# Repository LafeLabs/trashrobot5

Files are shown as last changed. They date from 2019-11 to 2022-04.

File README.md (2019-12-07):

## [link up a level../](../)

# Trash robot

## UNO Shield

[link to page on pcbway to buy board](https://www.pcbway.com/project/shareproject/Generic_Trash_Robot_UNO_Shield__V5.html)

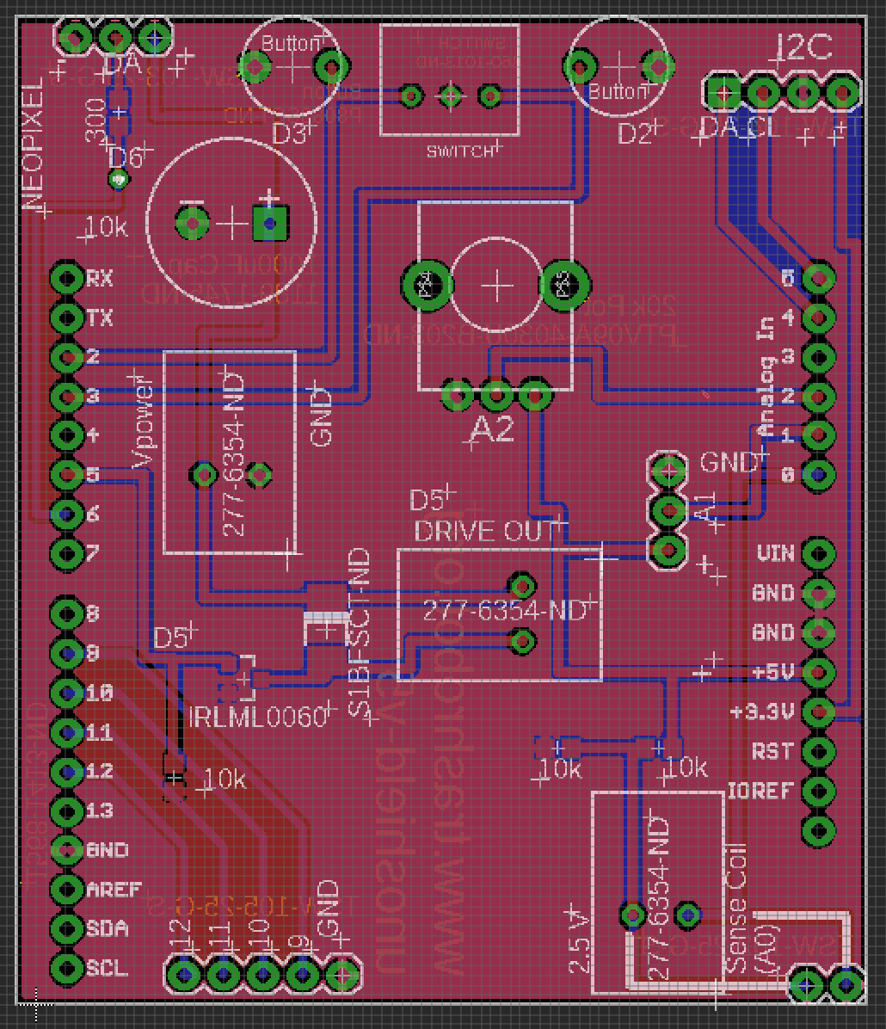
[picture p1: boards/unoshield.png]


## UNO Shield BOM

| REFDES|value| source/part#| 
|---|-----|---|
| R1  | 10k | [digikey RNCP0603FTD10K0CT-ND](https://www.digikey.com/product-detail/en/panasonic-electronic-components/ERJ-3EKF3301V/P3.30KHCT-ND/1746762)  | 
| R2  | 10k | [digikey RNCP0603FTD10K0CT-ND](https://www.digikey.com/product-detail/en/panasonic-electronic-components/ERJ-3EKF3301V/P3.30KHCT-ND/1746762)  | 
| R3  | 10k | [digikey RNCP0603FTD10K0CT-ND](https://www.digikey.com/product-detail/en/panasonic-electronic-components/ERJ-3EKF3301V/P3.30KHCT-ND/1746762)  | 
| R4  | 300 | [digikey RR08P300DCT-ND](https://www.digikey.com/product-detail/en/susumu/RR0816P-301-D/RR08P300DCT-ND/432711)  | 
| R5  |10k pot| [digikey PTV09A-4225F-B103-ND](https://www.digikey.com/product-detail/en/bourns-inc/PTV09A-4225F-B103/PTV09A-4225F-B103-ND/3781155)  | 
| Q1  |MOSFET| [digikey IRLML0060TRPBFCT-ND](https://www.digikey.com/product-detail/en/infineon-technologies/IRLML0060TRPBF/IRLML0060TRPBFCT-ND/2202229)  | 
| D1  |DIODE| [digikey S1BFSCT-ND](https://www.digikey.com/product-detail/en/on-semiconductor/S1B/S1BFSCT-ND/965719)  | 
| C1  |1000uF| [digikey 1189-1745-ND](https://www.digikey.com/product-detail/en/rubycon/35PX1000MEFC10X20/1189-1745-ND/3563769)  | 
| X1  |CONTACT| [digikey 277-6354-ND](https://www.digikey.com/product-detail/en/phoenix-contact/1984963/277-6354-ND/2513976)  | 
| X2  |CONTACT| [digikey 277-6354-ND](https://www.digikey.com/product-detail/en/phoenix-contact/1984963/277-6354-ND/2513976)  | 
| X3  |CONTACT| [digikey 277-6354-ND](https://www.digikey.com/product-detail/en/phoenix-contact/1984963/277-6354-ND/2513976)  | 
| SW1  |BUTTON| [digikey P15931SCT-ND](https://www.digikey.com/product-detail/en/panasonic-electronic-components/EVQ-11D05B/P15931SCT-ND/3873336)  | 
| SW2  |BUTTON| [digikey P15931SCT-ND](https://www.digikey.com/product-detail/en/panasonic-electronic-components/EVQ-11D05B/P15931SCT-ND/3873336)  | 
| SW3  |SPDT| [digikey 360-1013-ND](https://www.digikey.com/product-detail/en/nkk-switches/B13AP/360-1013-ND/379100)  | 
| J1  |3x HEADERS| [digikey SAM1029-03-ND](https://www.digikey.com/product-detail/en/samtec-inc/TSW-103-07-G-S/SAM1029-03-ND/1101324)| 
| J2  |4x HEADERS| [digikey SAM1029-04-ND](https://www.digikey.com/product-detail/en/samtec-inc/TSW-104-07-G-S/SAM1029-04-ND/1101323)| 
| J3  |5x HEADERS| [digikey SAM1029-05-ND](https://www.digikey.com/product-detail/en/samtec-inc/TSW-105-07-G-S/SAM1029-05-ND/1101322)| 
| J4  |ARDUINO HEADERS| [digikey 1528-1074-ND](https://www.digikey.com/product-detail/en/adafruit-industries-llc/85/1528-1074-ND/5154649)|
| JS1  |3X SOCKET| [digikey SAM1206-03-ND](https://www.digikey.com/product-detail/en/samtec-inc/SSQ-103-03-T-S/SAM1206-03-ND/1111955)|
| JS2  |4X SOCKET| [digikey SAM1206-04-ND](https://www.digikey.com/product-detail/en/samtec-inc/SSQ-104-03-T-S/SAM1206-04-ND/1111954)|
| JS3  |5X SOCKET| [digikey SAM1206-05-ND](https://www.digikey.com/product-detail/en/samtec-inc/SSQ-105-03-T-S/SAM1206-05-ND/1111953)|

## Dual H Bridge

[link to buy on PCBway](https://www.pcbway.com/project/shareproject/Dual_H_Bridge__V_5.html)

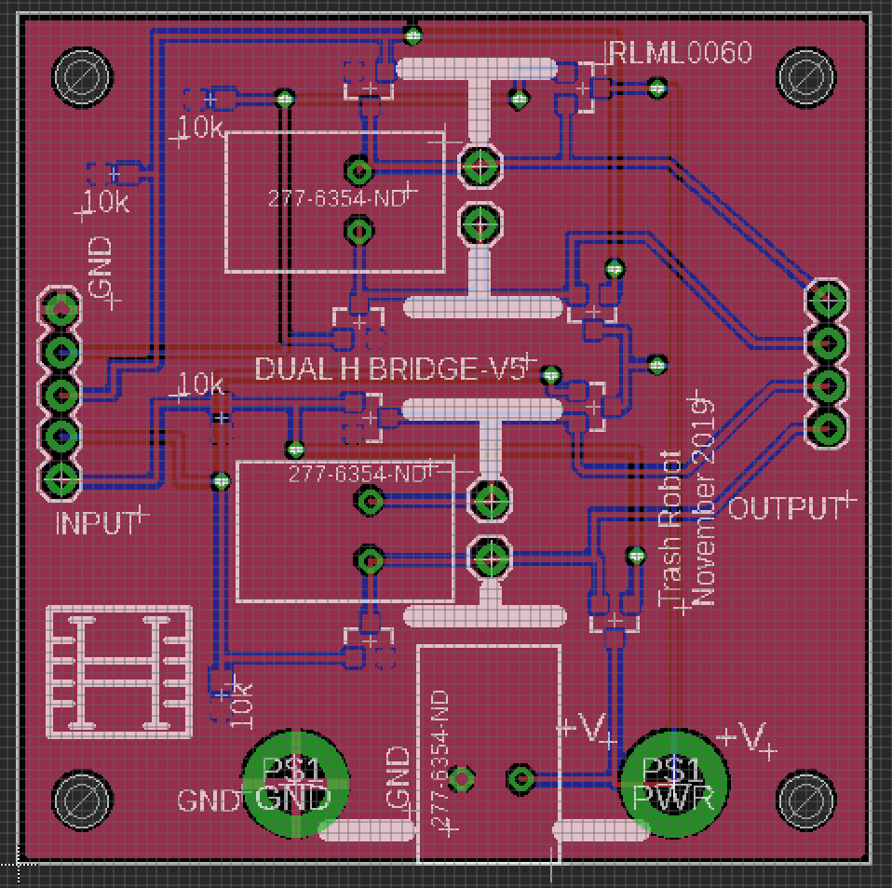
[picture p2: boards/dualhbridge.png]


## Dual H Bridge BOM

| REFDES|value| source/part#| 
|---|-----|---|
| R1  | 10k | [digikey RNCP0603FTD10K0CT-ND](https://www.digikey.com/product-detail/en/panasonic-electronic-components/ERJ-3EKF3301V/P3.30KHCT-ND/1746762)  | 
| R2  | 10k | [digikey RNCP0603FTD10K0CT-ND](https://www.digikey.com/product-detail/en/panasonic-electronic-components/ERJ-3EKF3301V/P3.30KHCT-ND/1746762)  | 
| R3  | 10k | [digikey RNCP0603FTD10K0CT-ND](https://www.digikey.com/product-detail/en/panasonic-electronic-components/ERJ-3EKF3301V/P3.30KHCT-ND/1746762)  | 
| R4  | 10k | [digikey RNCP0603FTD10K0CT-ND](https://www.digikey.com/product-detail/en/panasonic-electronic-components/ERJ-3EKF3301V/P3.30KHCT-ND/1746762)  | 
| Q1  |MOSFET| [digikey IRLML0060TRPBFCT-ND](https://www.digikey.com/product-detail/en/infineon-technologies/IRLML0060TRPBF/IRLML0060TRPBFCT-ND/2202229)  | 
| Q2  |MOSFET| [digikey IRLML0060TRPBFCT-ND](https://www.digikey.com/product-detail/en/infineon-technologies/IRLML0060TRPBF/IRLML0060TRPBFCT-ND/2202229)  | 
| Q3  |MOSFET| [digikey IRLML0060TRPBFCT-ND](https://www.digikey.com/product-detail/en/infineon-technologies/IRLML0060TRPBF/IRLML0060TRPBFCT-ND/2202229)  | 
| Q4  |MOSFET| [digikey IRLML0060TRPBFCT-ND](https://www.digikey.com/product-detail/en/infineon-technologies/IRLML0060TRPBF/IRLML0060TRPBFCT-ND/2202229)  | 
| Q5  |MOSFET| [digikey IRLML0060TRPBFCT-ND](https://www.digikey.com/product-detail/en/infineon-technologies/IRLML0060TRPBF/IRLML0060TRPBFCT-ND/2202229)  | 
| Q6  |MOSFET| [digikey IRLML0060TRPBFCT-ND](https://www.digikey.com/product-detail/en/infineon-technologies/IRLML0060TRPBF/IRLML0060TRPBFCT-ND/2202229)  | 
| Q7  |MOSFET| [digikey IRLML0060TRPBFCT-ND](https://www.digikey.com/product-detail/en/infineon-technologies/IRLML0060TRPBF/IRLML0060TRPBFCT-ND/2202229)  | 
| Q8  |MOSFET| [digikey IRLML0060TRPBFCT-ND](https://www.digikey.com/product-detail/en/infineon-technologies/IRLML0060TRPBF/IRLML0060TRPBFCT-ND/2202229)  | 
| X1  |CONTACT| [digikey 277-6354-ND](https://www.digikey.com/product-detail/en/phoenix-contact/1984963/277-6354-ND/2513976)  | 
| X2  |CONTACT| [digikey 277-6354-ND](https://www.digikey.com/product-detail/en/phoenix-contact/1984963/277-6354-ND/2513976)  | 
| X3  |CONTACT| [digikey 277-6354-ND](https://www.digikey.com/product-detail/en/phoenix-contact/1984963/277-6354-ND/2513976)  | 
| J1  |4x RA HEADERS| [digikey TSW-104-25-G-S-RA-ND](https://www.digikey.com/product-detail/en/samtec-inc/TSW-104-25-G-S-RA/TSW-104-25-G-S-RA-ND/7864906)| 
| J2  |5x RA HEADERS| [digikey TSW-105-25-G-S-RA-ND](https://www.digikey.com/product-detail/en/samtec-inc/TSW-105-25-G-S-RA/TSW-105-25-G-S-RA-ND/2685928)| 
| JS1  |4X SOCKET| [digikey SAM1206-04-ND](https://www.digikey.com/product-detail/en/samtec-inc/SSQ-104-03-T-S/SAM1206-04-ND/1111954)|
| JS2  |5X SOCKET| [digikey SAM1206-05-ND](https://www.digikey.com/product-detail/en/samtec-inc/SSQ-105-03-T-S/SAM1206-05-ND/1111953)|

## Kit BOM

|Description|Link|
|---|----|
|Jumper Wires|[Digikey 1528-1160-ND](https://www.digikey.com/product-detail/en/adafruit-industries-llc/824/1528-1160-ND/5353620)|
|Solder Paste|[Digikey SMDLTLFP-ND](https://www.digikey.com/product-detail/en/chip-quik-inc/SMDLTLFP/SMDLTLFP-ND/2682721)|
|2.1X5 MM Barrel Breakout|[Digikey 839-1518-ND](https://www.digikey.com/product-detail/en/tensility-international-corp/10-02931/839-1518-ND/9686414)|
|2.1X5 MM Barrel patch cable|[Amazon $6.99](https://www.amazon.com/Valley-Enterprises%C2%AE-2-1mm-5-5mm-Adapter/dp/B00DX72UXW/)|
| 12V 12Ah LiPo|[Amazon $33.99](https://www.amazon.com/gp/product/B00ME3ZH7C/)|
| 12V 3Ah LiPo |[Amazon $24.19](https://www.amazon.com/TalentCell-Rechargeable-3000mAh-Lithium-External/dp/B01M7Z9Z1N/) |
|30 AWG Magnet wire|[Amazon $17.45](https://www.amazon.com/dp/B07SG4CPSF/) |
| Arduino Uno | [Amazon $8.49](https://www.amazon.com/HiLetgo-ATmega328P-Development-Compatible-Microcontroller/dp/B01AR7YJ3O/) |
| Hookup Wire Kit | [Adafruit $19.95](https://www.adafruit.com/product/3111) |
| 3 axis Accelerometer | [Adafruit $7.95](https://www.adafruit.com/product/2019) |
| I2C Pressure Sensor| [Adafruit $9.95](https://www.adafruit.com/product/2651) |
|ultrasonic range finder|[Sparkfun $3.95](https://www.sparkfun.com/products/15569)|
| Neopixel 8x array| [Adafruit $5.95](https://www.adafruit.com/product/1426) |
| Hot Air Rework Tool| [Sparkfun $129.95](https://www.sparkfun.com/products/14557) |
| Soldering Iron| [Sparkfun $129.00](https://www.sparkfun.com/products/14734) |
| Lead Free Solder| [Sparkfun $7.95](https://www.sparkfun.com/products/9325) |

- [boards/unoshield-v5.brd](boards/unoshield-v5.brd)
- [boards/unoshield-v5.sch](boards/unoshield-v5.sch)
- [boards/unoshield-v5-bom.xlsx](boards/unoshield-v5-bom.xlsx)
- [boards/dualHbridge-v5.brd](boards/dualHbridge-v5.brd)
- [boards/dualHbridge-v5.sch](boards/dualHbridge-v5.sch)
- [boards/dualHbridge-v5bom.xlsx](boards/dualHbridge-v5bom.xlsx)

### Cables:

- 4 conductor, 8 inches long, header to stripped and tinned ends with 1/4 inch stripping: [IDSS-04-S-08.00-ST4](https://www.samtec.com/products/idss-04-s-08.00-st4)
- 3 conductor, 8 inches long, header to stripped and tinned ends, with 1/4 inch stripping: [https://www.samtec.com/products/idss-03-s-08.00-st4](https://www.samtec.com/products/idss-03-s-08.00-st4)

# 90 degree terminal strips for dual h bridge:

5 pin:
TSW-105-25-G-S-RA	



4 pin:

TSW-104-25-G-S-RA

## 5 wire cable from shield to dual h bridge:

idss-05-d-06.00



## 4 wire cable to solder stripped ends for stepper motor and also I2C sensors(need as many of these as stepper motors plus I2 C sensors.):

IDSS-04-S-08.00-T	(8 inches)



## 3 wire cable with solder tinned ends for neopixels, 8 inch:

IDSS-03-S-08.00-T

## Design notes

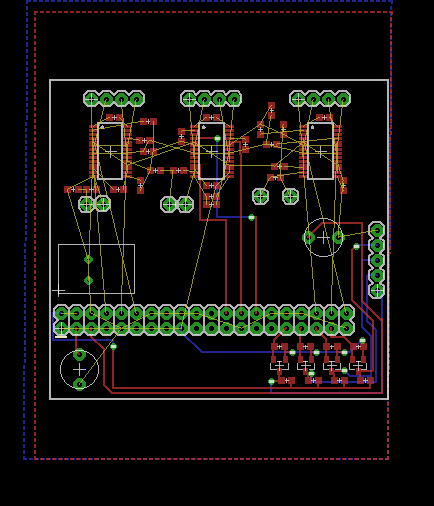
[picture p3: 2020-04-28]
boards/capture.png

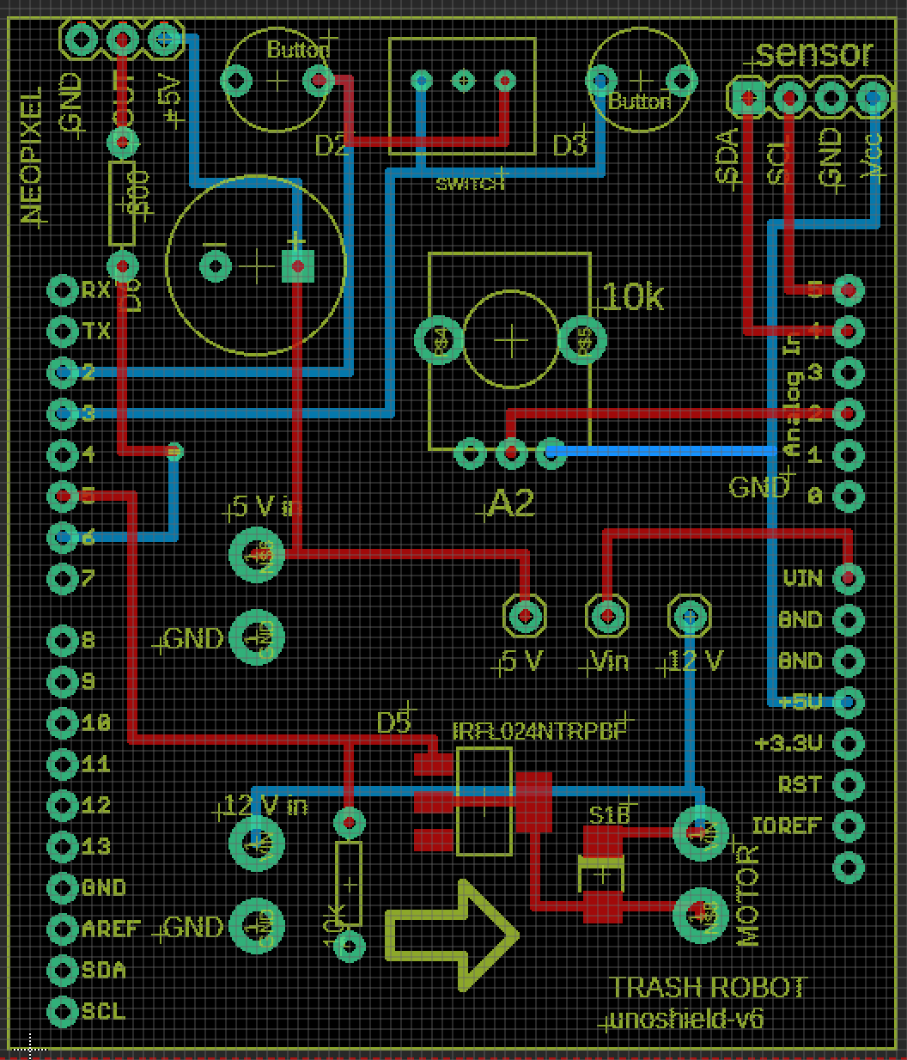
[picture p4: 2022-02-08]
boards/unoshield-v6-screenshot.png

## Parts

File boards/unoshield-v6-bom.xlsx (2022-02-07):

REFDES | Value | QTY | Manufacturer | Manufacturer Part Number | Digikey Part Number | package | Price
Q1 |  | 1 | Infineon | IRFL024NTRPBF | IRFL024NTRPBFCT-ND | SOT-223 | $0.50
D1 |  | 1 | ON semiconductor | S1B | S1BFSCT-ND | DO-214AC | $0.20
R1 | 10k | 1 | stackpole electronics | ERJ-3EKF3301V | RNCP0603FTD10K0CT-ND | axial | $0.02
R1 | 300 | 1 | Stackpole electronics | CF18JA300R | CF18JA300RCT-ND | axial | $0.02
R3 | 10k pot | 1 | Bourns, inc | PTV09A-4225F-B103 | PTV09A-4225F-B103-ND |  | $0.75
C1 | 1000uF | 1 | Rubycon | 35PX1000MEFC10X20 | 1189-1745-ND | can | $0.51
SW1 | button | 2 | E-switch | TL59AF100Q | EG4378CT-ND |  | $0.27
SW2 | button |  | E-switch | TL59AF100Q | EG4378CT-ND |  | $0.23
SW3 | switches | 1 | NKK switches | B13AP | 360-1013-ND |  | $3.50
Jx | headers | 40 pins | adafruit | 392 | - |  | $1.00
Pcb |  |  | Pcbway.com |  |  |  | $2.00
total |  |  |  |  |  |  | $9.00
 | -

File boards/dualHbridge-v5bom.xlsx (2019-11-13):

REFDES | Value | QTY | Manufacturer | Manufacturer Part Number | Digikey Part Number | package | Price
Q1 | IRLML0060 | 1 | Infineon | IRLML0060 | IRLML0060TRPBFCT-ND |  | $0.25
Q2 | IRLML0060 | 1 | Infineon | IRLML0060 | IRLML0060TRPBFCT-ND |  | $0.25
Q3 | IRLML0060 | 1 | Infineon | IRLML0060 | IRLML0060TRPBFCT-ND |  | $0.25
Q4 | IRLML0060 | 1 | Infineon | IRLML0060 | IRLML0060TRPBFCT-ND |  | $0.25
Q5 | IRLML0060 | 1 | Infineon | IRLML0060 | IRLML0060TRPBFCT-ND |  | $0.25
Q6 | IRLML0060 | 1 | Infineon | IRLML0060 | IRLML0060TRPBFCT-ND |  | $0.25
Q7 | IRLML0060 | 1 | Infineon | IRLML0060 | IRLML0060TRPBFCT-ND |  | $0.25
Q8 | IRLML0060 | 1 | Infineon | IRLML0060 | IRLML0060TRPBFCT-ND |  | $0.25
X1 | spring contact | 3 | Phoenix Contact | 1984963 | 277-6354-ND
X2 |  |  | Phoenix Contact | 1984963 | 277-6354-ND
X3 |  |  | Phoenix Contact | 1984963 | 277-6354-ND
R1 | 10k | 4 | stackpole electronics | ERJ-3EKF3301V | RNCP0603FTD10K0CT-ND | 0603 | $0.03
R2 | 10k |  | stackpole electronics | ERJ-3EKF3301V | RNCP0603FTD10K0CT-ND | 0603 | $0.03
R3 | 10k |  | stackpole electronics | ERJ-3EKF3301V | RNCP0603FTD10K0CT-ND | 0603 | $0.03
R4 | 10k |  | stackpole electronics | ERJ-3EKF3301V | RNCP0603FTD10K0CT-ND | 0603 | $0.03
J1 | 4 pin header | 1 | Samtec | TSW-104-25-G-S-RA |  |  | $0.25
J1 | 5 pin header | 1 | Samtec | TSW-105-25-G-S-RA |  |  | $0.25
total |  |  |  |  |  |  | $2.00

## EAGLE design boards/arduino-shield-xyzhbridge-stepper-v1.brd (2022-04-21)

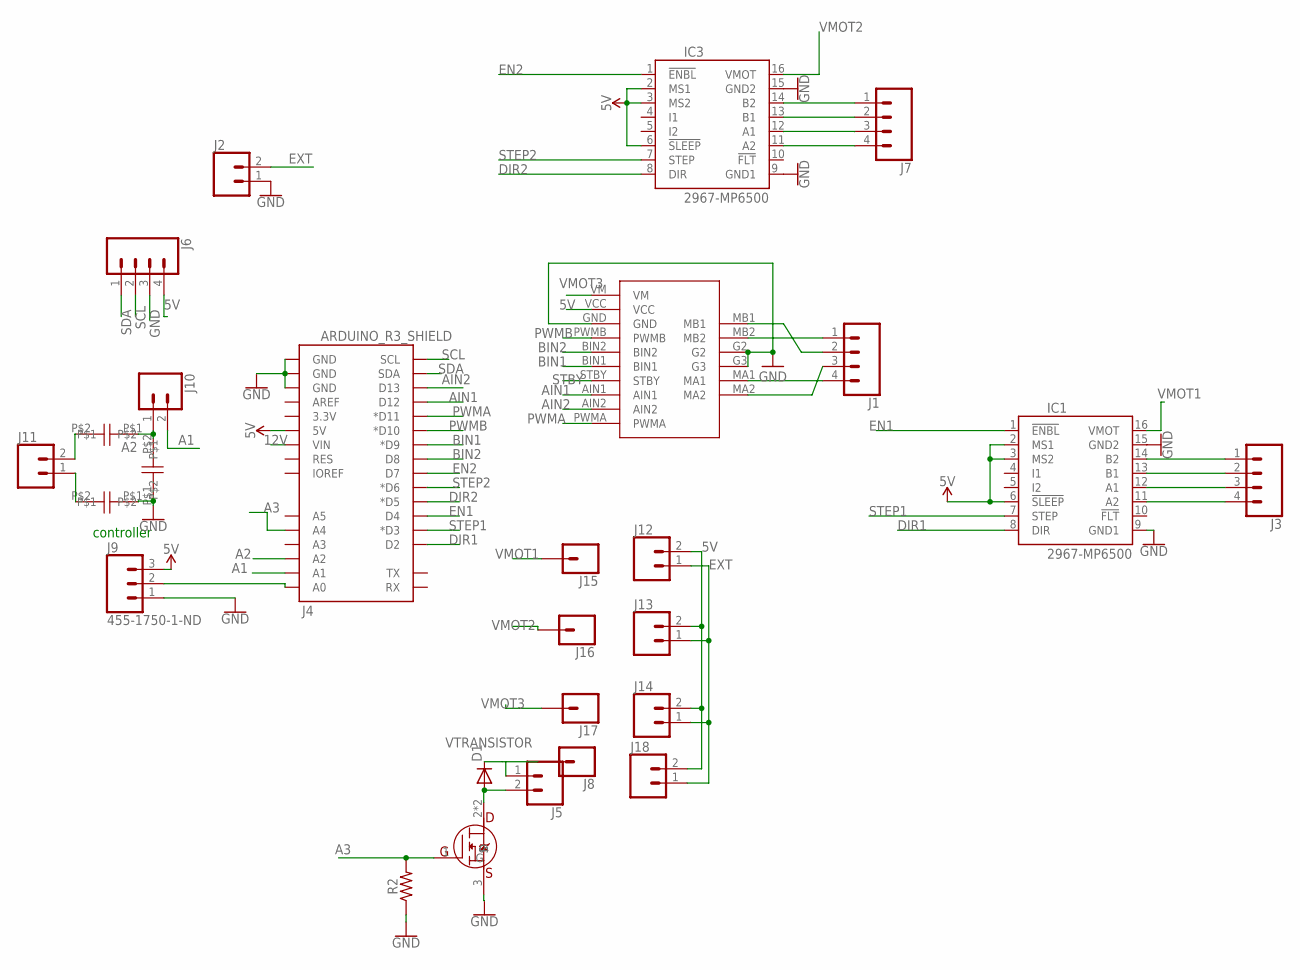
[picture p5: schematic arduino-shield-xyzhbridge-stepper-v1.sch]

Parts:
D1: DIODE-DO-214AC; DO-214AC
IC1, IC3: 2967-MP6500; MP6500
J1, J3, J6, J7: CONN_04; 1X04
J2, J5, J10, J11, J12, J13, J14, J18: CONN_02; 1X02
J4: ARDUINO_R3_SHIELD; UNO_R3_SHIELD
J8, J15, J16, J17: CONN_01; 1X01
J9: 455-1750-1-ND; 1X03
R2: AXIAL-0.3
U$1: ADAFRUIT-TB6612
U$2, U$3, U$4: AXIALCAP
U$5: IRFL024NPBF; SOT223

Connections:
5V: IC1.2 (MS1), IC1.3 (MS2), IC1.6 (!SLEEP), IC3.2 (MS1), IC3.3 (MS2), IC3.6 (!SLEEP), J4.5V, J6.4, J9.3, J12.2, J13.2, J14.2, J18.2, U$1.VCC
12V: J4.VIN
A1: J4.A1, J10.2
A2: J4.A2, J10.1, U$3.P$2, U$4.P$1
A3: J4.A4, R2.P$2 (2), U$5.1 (G)
AIN1: J4.D12, U$1.AIN1
AIN2: J4.D13, U$1.AIN2
BIN1: J4.D9 (*D9), U$1.BIN1
BIN2: J4.D8, U$1.BIN2
DIR1: IC1.8 (DIR), J4.D2
DIR2: IC3.8 (DIR), J4.D5 (*D5)
EN1: IC1.1 (!ENBL), J4.D4
EN2: IC3.1 (!ENBL), J4.D7
EXT: J2.2, J12.1, J13.1, J14.1, J18.1
GND: IC1.9 (GND1), IC1.15 (GND2), IC3.9 (GND1), IC3.15 (GND2), J2.1, J4.GND@0 (GND), J4.GND@1 (GND), J4.GND@2 (GND), J6.3, J9.1, R2.P$1 (1), U$1.G2, U$1.G3, U$1.GND, U$2.P$1, U$3.P$1, U$5.3 (S)
unnamed: IC3.14 (B2), J7.1
unnamed: IC3.13 (B1), J7.2
unnamed: IC1.14 (B2), J3.1
unnamed: IC1.13 (B1), J3.2
unnamed: IC1.12 (A1), J3.3
unnamed: IC1.11 (A2), J3.4
unnamed: J1.2, U$1.MB1
unnamed: J1.1, U$1.MB2
unnamed: IC3.12 (A1), J7.3
unnamed: IC3.11 (A2), J7.4
unnamed: J4.A0, J9.2
unnamed: J1.4, U$1.MA1
unnamed: J1.3, U$1.MA2
unnamed: D1.A, J5.2, U$5.2 (D), U$5.4 (D)
unnamed: J11.2, U$4.P$2
unnamed: J11.1, U$2.P$2
PWMA: J4.D11 (*D11), U$1.PWMA
PWMB: J4.D10 (*D10), U$1.PWMB
SCL: J4.SCL, J6.2
SDA: J4.SDA, J6.1
STBY: U$1.STBY
STEP1: IC1.7 (STEP), J4.D3 (*D3)
STEP2: IC3.7 (STEP), J4.D6 (*D6)
VMOT1: IC1.16 (VMOT), J15.1
VMOT2: IC3.16 (VMOT), J16.1
VMOT3: J17.1, U$1.VM
VTRANSISTOR: D1.C, J5.1, J8.1

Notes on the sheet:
controller

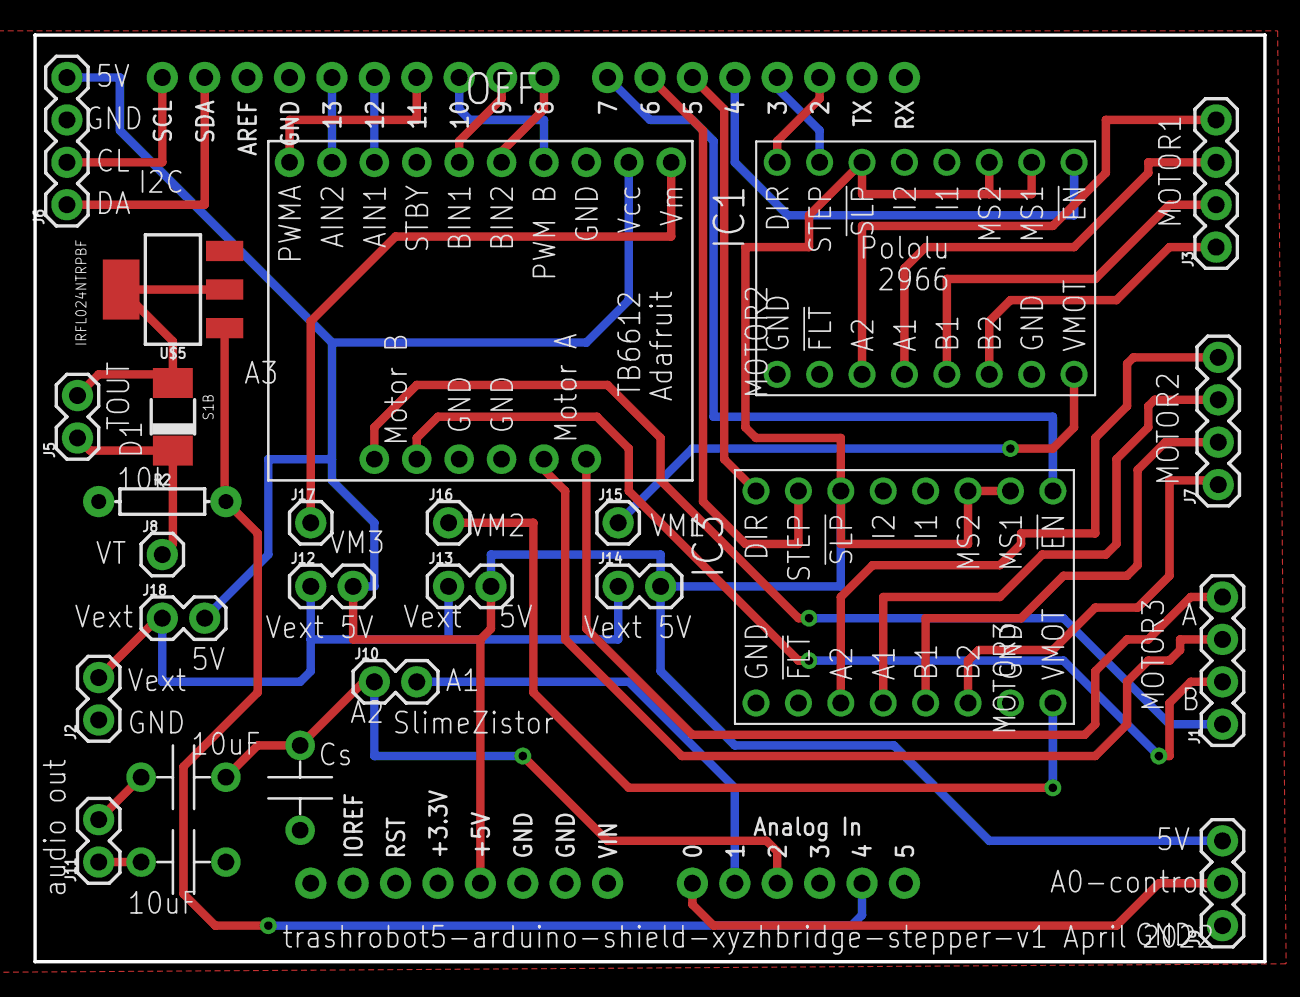
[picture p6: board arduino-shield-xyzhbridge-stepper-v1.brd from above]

Board: 2 copper layers, 73.7 x 55.5 mm, 27 parts (0 on the bottom side), 40 nets.

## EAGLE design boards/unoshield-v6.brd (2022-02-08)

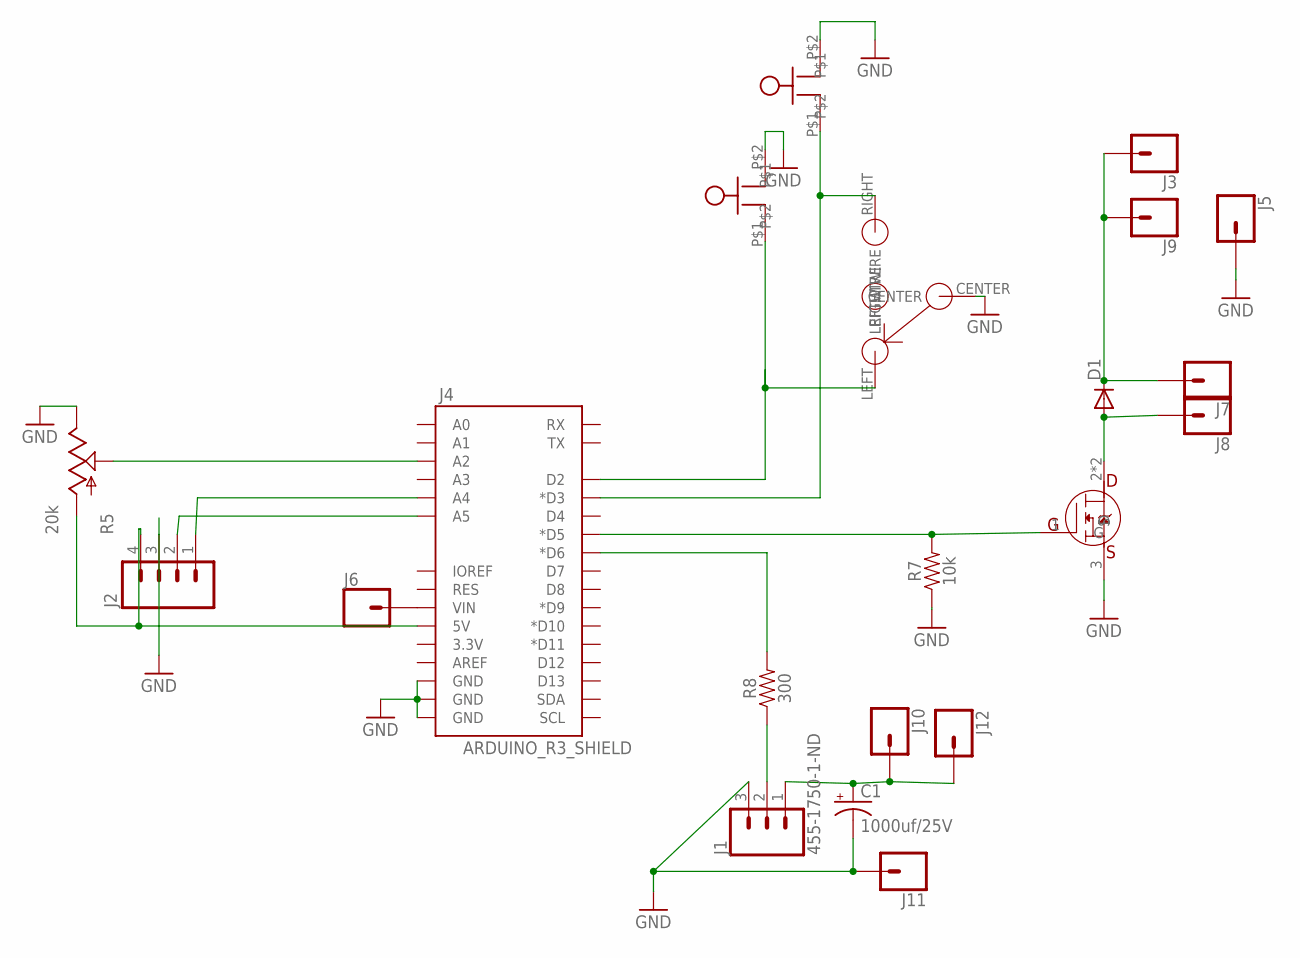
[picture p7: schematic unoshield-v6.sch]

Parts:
C1: 1000uf/25V; CPOL-RADIAL-1000UF-25V-KIT
D1: DIODE-DO-214AC; DO-214AC
J1: 455-1750-1-ND; 1X03
J2: M04PTH; 1X04
J3, J5, J7, J8, J10, J11: CONN_01PTH_2MM; 1X01_2MM
J4: ARDUINO_R3_SHIELD; UNO_R3_SHIELD
J6, J9, J12: CONN_01; 1X01
R5: 20k; ALPS_POT_KIT
R7: 10k; AXIAL-0.3
R8: 300; AXIAL-0.3
SW1, SW2: BUTTON
SW3: ON-OFF-ON-360-1013-ND; 360-1013-ND
U$1: IRFL024NPBF; SOT223

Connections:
BUTTON: J4.D3 (*D3), SW2.P$1, SW3.RIGHT (RIGHTWIRE)
CL: J2.2, J4.A5
DA: J2.1, J4.A4
GND: C1.-, J1.3, J2.3, J4.GND@0 (GND), J4.GND@1 (GND), J4.GND@2 (GND), J5.1, J11.1, R5.P$1 (E), R7.P$1 (1), SW1.P$2, SW2.P$2, SW3.CENTER, U$1.3 (S)
unnamed: J4.D5 (*D5), R7.P$2 (2), U$1.1 (G)
unnamed: J4.D6 (*D6), R8.P$2 (2)
unnamed: J4.VIN, J6.1
unnamed: C1.+, J1.1, J10.1, J12.1
unnamed: D1.A, J8.1, U$1.2 (D), U$1.4 (D)
unnamed: J4.D2, SW1.P$1, SW3.LEFT (LEFTWIRE)
unnamed: J1.2, R8.P$1 (1)
unnamed: J4.A2, R5.P$2 (S)
VCC: J2.4, J4.5V, R5.P$3 (A)
VIN: D1.C, J3.1, J7.1, J9.1

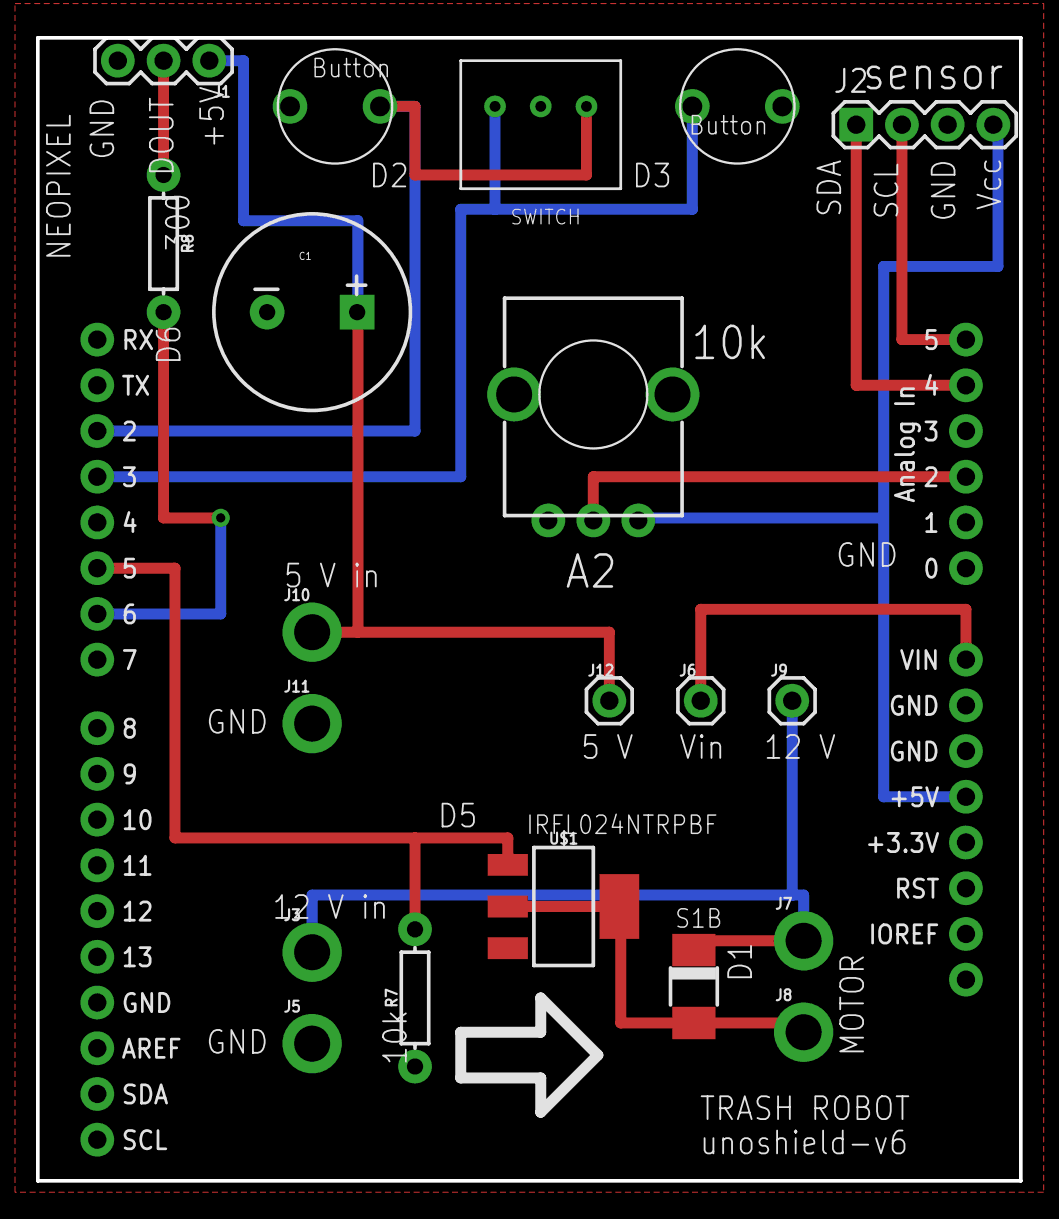
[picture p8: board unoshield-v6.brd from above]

Board: 2 copper layers, 54.6 x 63.5 mm, 21 parts (0 on the bottom side), 14 nets.

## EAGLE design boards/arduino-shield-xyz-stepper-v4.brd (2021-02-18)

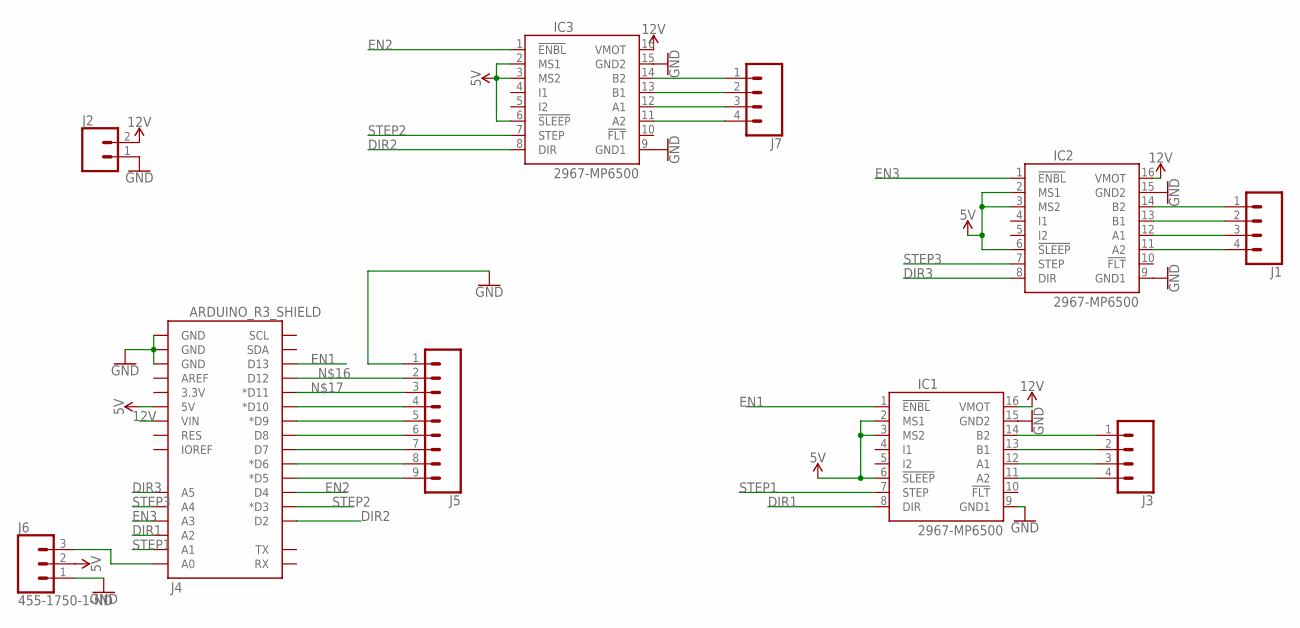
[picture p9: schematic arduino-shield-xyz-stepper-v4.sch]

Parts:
IC1, IC2, IC3: 2967-MP6500; MP6500
J1, J3, J7: CONN_04; 1X04
J2: CONN_02; 1X02
J4: ARDUINO_R3_SHIELD; UNO_R3_SHIELD
J5: CONN_09; 1X09
J6: 455-1750-1-ND; 1X03

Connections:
5V: IC1.2 (MS1), IC1.3 (MS2), IC1.6 (!SLEEP), IC2.2 (MS1), IC2.3 (MS2), IC2.6 (!SLEEP), IC3.2 (MS1), IC3.3 (MS2), IC3.6 (!SLEEP), J4.5V, J6.2
12V: IC1.16 (VMOT), IC2.16 (VMOT), IC3.16 (VMOT), J2.2, J4.VIN
DIR1: IC1.8 (DIR), J4.A2
DIR2: IC3.8 (DIR), J4.D2
DIR3: IC2.8 (DIR), J4.A5
EN1: IC1.1 (!ENBL), J4.D13
EN2: IC3.1 (!ENBL), J4.D4
EN3: IC2.1 (!ENBL), J4.A3
GND: IC1.9 (GND1), IC1.15 (GND2), IC2.9 (GND1), IC2.15 (GND2), IC3.9 (GND1), IC3.15 (GND2), J2.1, J4.GND@0 (GND), J4.GND@1 (GND), J4.GND@2 (GND), J5.1, J6.1
unnamed: IC3.14 (B2), J7.1
unnamed: IC3.13 (B1), J7.2
unnamed: IC1.14 (B2), J3.1
unnamed: IC1.13 (B1), J3.2
unnamed: IC1.12 (A1), J3.3
unnamed: IC1.11 (A2), J3.4
unnamed: IC2.14 (B2), J1.1
unnamed: IC2.13 (B1), J1.2
unnamed: IC2.12 (A1), J1.3
unnamed: IC2.11 (A2), J1.4
unnamed: IC3.12 (A1), J7.3
unnamed: IC3.11 (A2), J7.4
unnamed: J4.A0, J6.3
unnamed: J4.D12, J5.2
unnamed: J4.D11 (*D11), J5.3
unnamed: J4.D10 (*D10), J5.4
unnamed: J4.D9 (*D9), J5.5
unnamed: J4.D8, J5.6
unnamed: J4.D7, J5.7
unnamed: J4.D6 (*D6), J5.8
unnamed: J4.D5 (*D5), J5.9
STEP1: IC1.7 (STEP), J4.A1
STEP2: IC3.7 (STEP), J4.D3 (*D3)
STEP3: IC2.7 (STEP), J4.A4

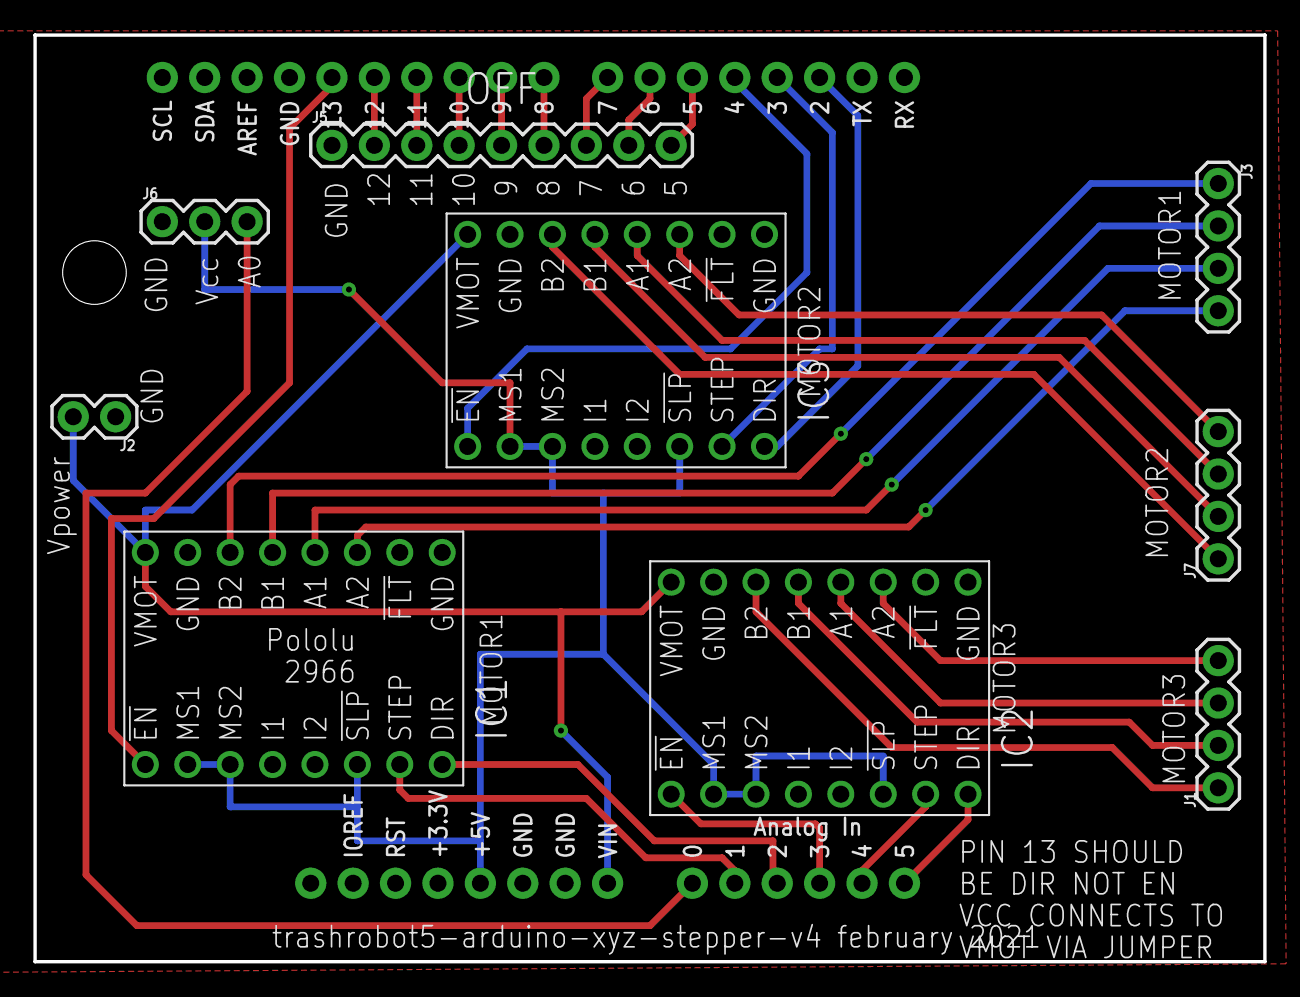
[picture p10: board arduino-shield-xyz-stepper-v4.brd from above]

Board: 2 copper layers, 73.7 x 55.5 mm, 10 parts (0 on the bottom side), 33 nets.

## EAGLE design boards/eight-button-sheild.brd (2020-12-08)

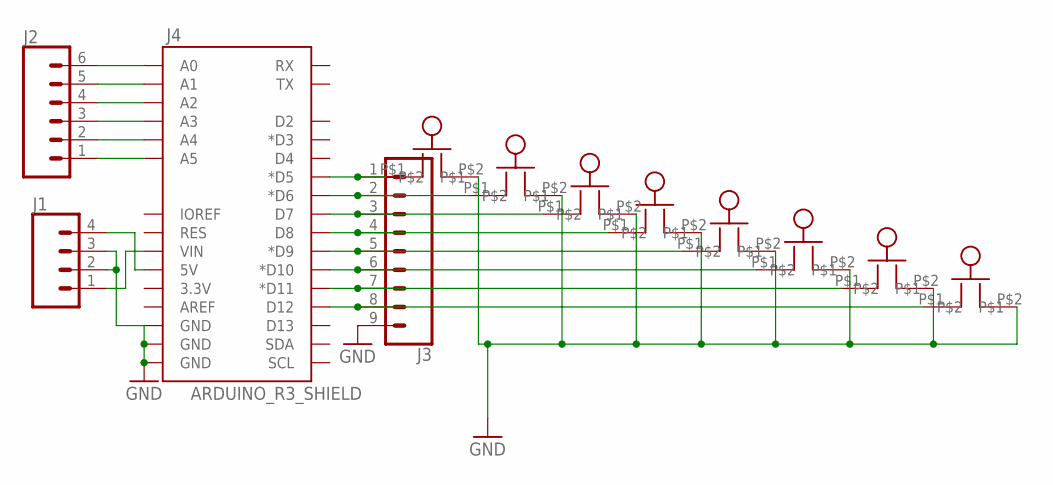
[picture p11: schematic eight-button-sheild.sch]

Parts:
J1: CONN_04; 1X04
J2: CONN_06SILK_FEMALE_PTH; 1X06
J3: CONN_09; 1X09
J4: ARDUINO_R3_SHIELD; UNO_R3_SHIELD
SW1, SW2, SW3, SW4, SW5, SW6, SW7, SW8: BUTTON

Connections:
GND: J1.2, J1.3, J3.9, J4.GND@0 (GND), J4.GND@1 (GND), J4.GND@2 (GND), SW1.P$2, SW2.P$2, SW3.P$2, SW4.P$2, SW5.P$2, SW6.P$2, SW7.P$2, SW8.P$2
unnamed: J3.1, J4.D5 (*D5), SW1.P$1
unnamed: J3.2, J4.D6 (*D6), SW2.P$1
unnamed: J3.3, J4.D7, SW3.P$1
unnamed: J3.4, J4.D8, SW4.P$1
unnamed: J3.5, J4.D9 (*D9), SW5.P$1
unnamed: J3.6, J4.D10 (*D10), SW6.P$1
unnamed: J2.1, J4.A5
unnamed: J3.7, J4.D11 (*D11), SW7.P$1
unnamed: J3.8, J4.D12, SW8.P$1
unnamed: J2.2, J4.A4
unnamed: J2.3, J4.A3
unnamed: J2.4, J4.A2
unnamed: J2.5, J4.A1
unnamed: J2.6, J4.A0
unnamed: J1.1, J4.VIN
unnamed: J1.4, J4.5V

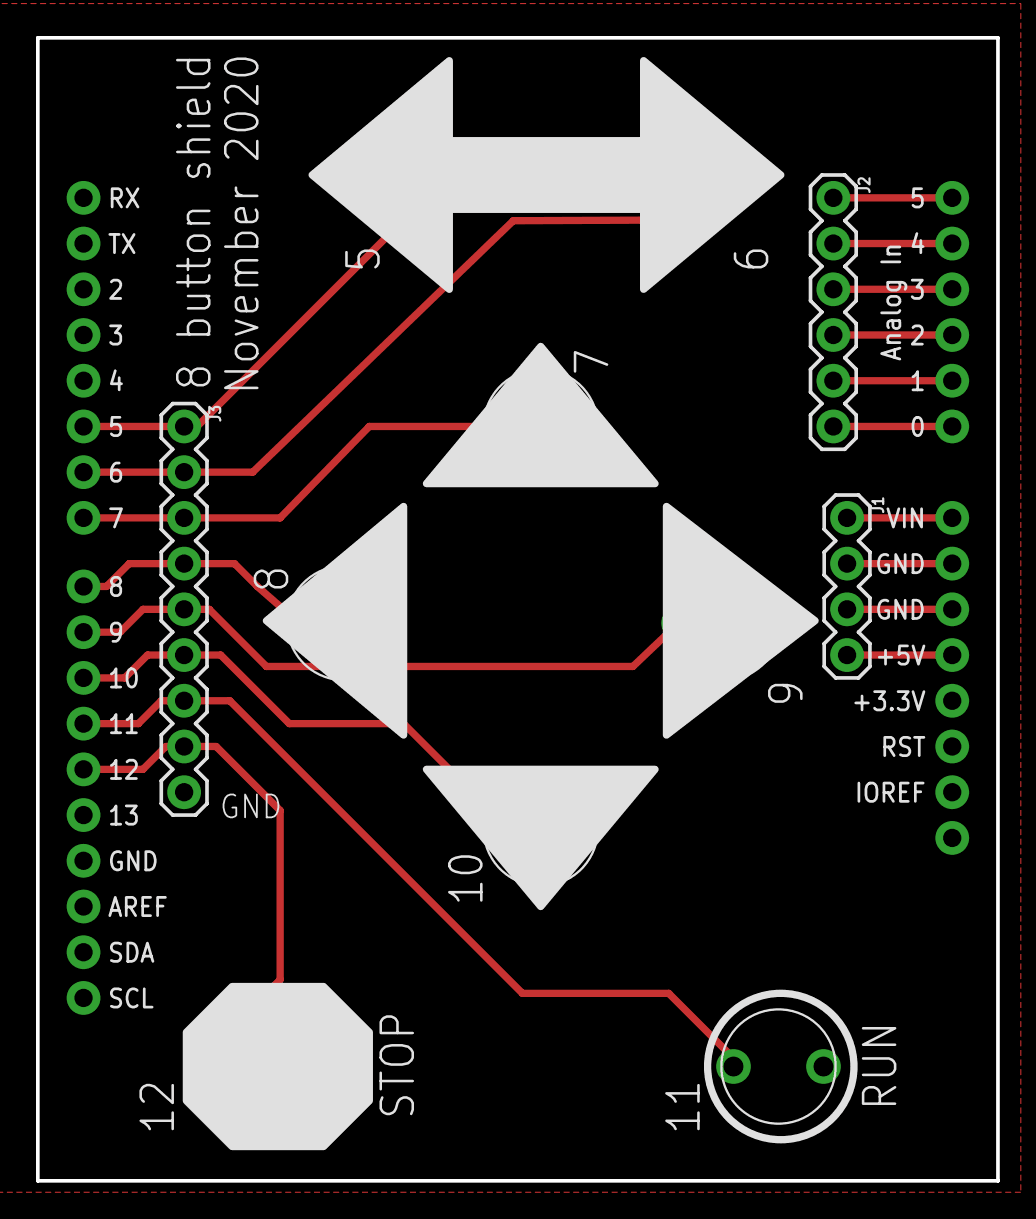
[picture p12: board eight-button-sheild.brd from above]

Board: 2 copper layers, 53.3 x 63.5 mm, 12 parts (0 on the bottom side), 17 nets.

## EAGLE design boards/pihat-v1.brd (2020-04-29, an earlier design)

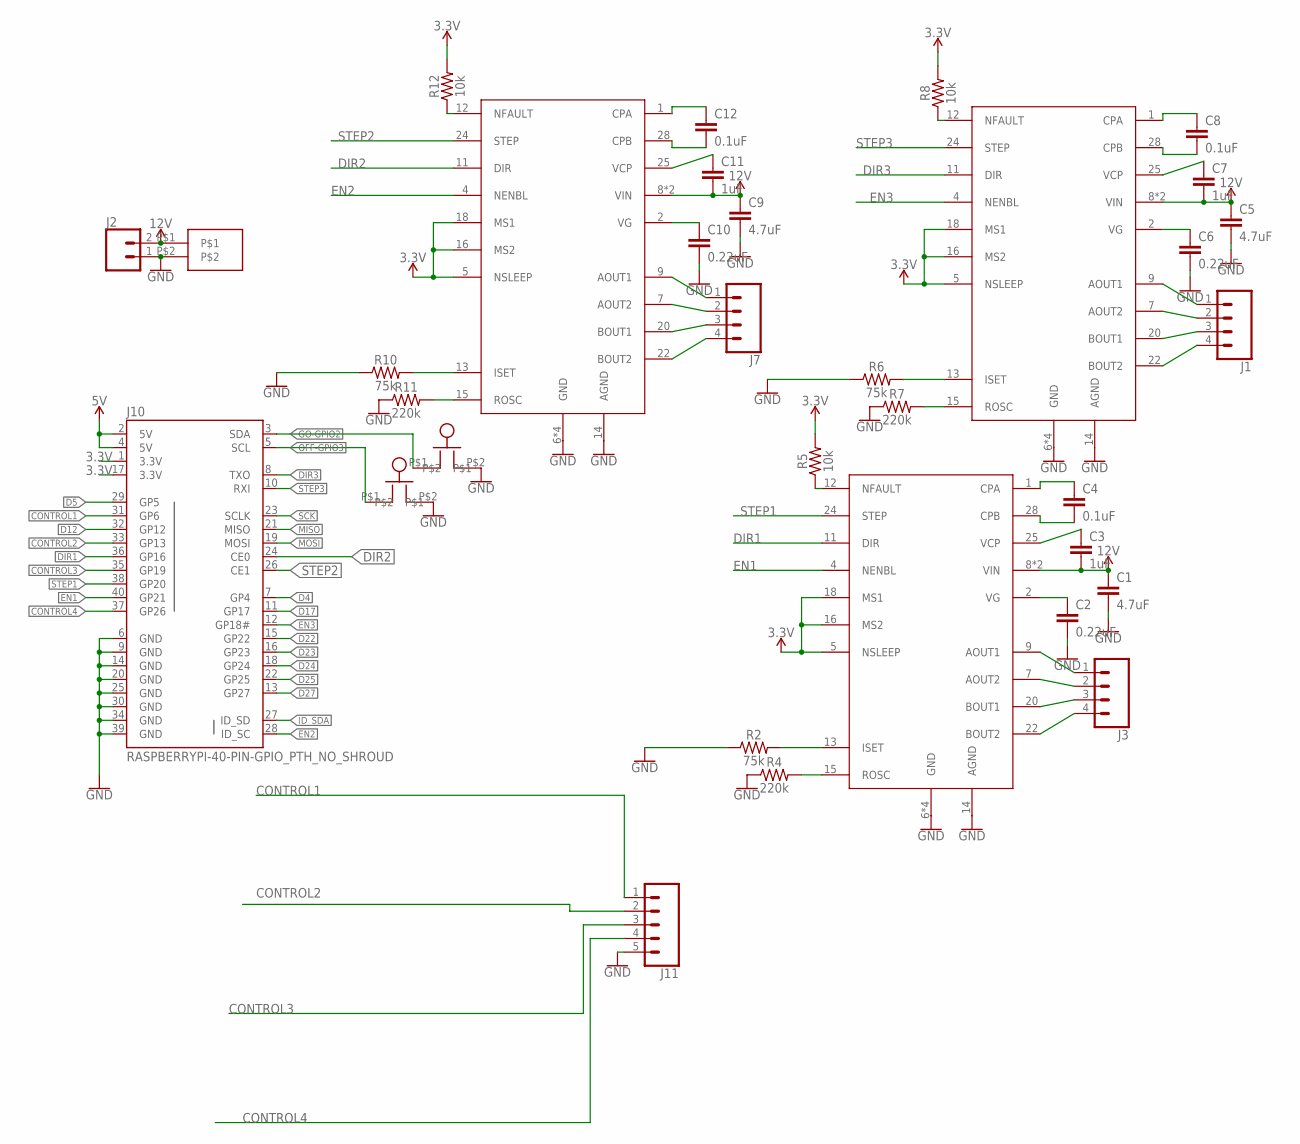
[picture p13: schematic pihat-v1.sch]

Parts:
C1, C5, C9: 4.7uF; 0603
C2, C6, C10: 0.22uF; 0603
C3, C7, C11: 1uF; 0603
C4, C8, C12: 0.1uF; 0603
J1, J3, J7: CONN_04; 1X04
J2: CONN_02; 1X02
J10: RASPBERRYPI-40-PIN-GPIO_PTH_NO_SHROUD; 2X20
J11: CONN_05; 1X05
R2, R6, R10: 75k; 0603
R4, R7, R11: 220k; 0603
R5, R8, R12: 10k; 0603
U$1, U$2, U$3: MP6500MP6500; TSSOP28
U$4, U$5: BUTTON
U$6: SPRING-TERMINAL

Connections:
3.3V: J10.1 (3.3V), J10.17 (3.3V), R5.2, R8.2, R12.2, U$1.5 (NSLEEP), U$1.16 (MS2), U$1.18 (MS1), U$2.5 (NSLEEP), U$2.16 (MS2), U$2.18 (MS1), U$3.5 (NSLEEP), U$3.16 (MS2), U$3.18 (MS1)
5V: J10.2 (5V), J10.4 (5V)
12V: C1.1, C3.2, C5.1, C7.2, C9.1, C11.2, J2.2, U$1.8 (VIN), U$1.21 (VIN), U$2.8 (VIN), U$2.21 (VIN), U$3.8 (VIN), U$3.21 (VIN), U$6.P$1
CONTROL1: J10.31 (GP6), J11.1
CONTROL2: J10.33 (GP13), J11.2
CONTROL3: J10.35 (GP19), J11.3
CONTROL4: J10.37 (GP26), J11.4
D4: J10.7 (GP4)
D5: J10.29 (GP5)
D12: J10.32 (GP12)
D17: J10.11 (GP17)
D22: J10.15 (GP22)
D23: J10.16 (GP23)
D24: J10.18 (GP24)
D25: J10.22 (GP25)
D27: J10.13 (GP27)
DIR1: J10.36 (GP16), U$3.11 (DIR)
DIR2: J10.24 (CE0), U$2.11 (DIR)
DIR3: J10.8 (TXO), U$1.11 (DIR)
EN1: J10.40 (GP21), U$3.4 (NENBL)
EN2: J10.28 (ID_SC), U$2.4 (NENBL)
EN3: J10.12 (GP18#), U$1.4 (NENBL)
GND: C1.2, C2.2, C5.2, C6.2, C9.2, C10.2, J2.1, J10.6 (GND), J10.9 (GND), J10.14 (GND), J10.20 (GND), J10.25 (GND), J10.30 (GND), J10.34 (GND), J10.39 (GND), J11.5, R2.1, R4.1, R6.1, R7.1, R10.1, R11.1, U$1.6 (GND), U$1.10 (GND), U$1.14 (AGND), U$1.19 (GND), U$1.23 (GND), U$2.6 (GND), U$2.10 (GND), U$2.14 (AGND), U$2.19 (GND), U$2.23 (GND), U$3.6 (GND), U$3.10 (GND), U$3.14 (AGND), U$3.19 (GND), U$3.23 (GND), U$4.P$2, U$5.P$2, U$6.P$2
GO-GPIO2: J10.3 (SDA), U$4.P$1
ID_SDA: J10.27 (ID_SD)
MISO: J10.21 (MISO)
MOSI: J10.19 (MOSI)
unnamed: J3.1, U$3.9 (AOUT1)
unnamed: J3.2, U$3.7 (AOUT2)
unnamed: J3.3, U$3.20 (BOUT1)
unnamed: J3.4, U$3.22 (BOUT2)
unnamed: J1.1, U$1.9 (AOUT1)
unnamed: J1.2, U$1.7 (AOUT2)
unnamed: J1.3, U$1.20 (BOUT1)
unnamed: J1.4, U$1.22 (BOUT2)
unnamed: C7.1, U$1.25 (VCP)
unnamed: C6.1, U$1.2 (VG)
unnamed: C8.1, U$1.1 (CPA)
unnamed: C8.2, U$1.28 (CPB)
unnamed: R5.1, U$3.12 (NFAULT)
unnamed: C3.1, U$3.25 (VCP)
unnamed: C2.1, U$3.2 (VG)
unnamed: C4.1, U$3.1 (CPA)
unnamed: C4.2, U$3.28 (CPB)
unnamed: R2.2, U$3.13 (ISET)
unnamed: R4.2, U$3.15 (ROSC)
unnamed: R7.2, U$1.15 (ROSC)
unnamed: R8.1, U$1.12 (NFAULT)
unnamed: R6.2, U$1.13 (ISET)
unnamed: J7.1, U$2.9 (AOUT1)
unnamed: J7.2, U$2.7 (AOUT2)
unnamed: J7.3, U$2.20 (BOUT1)
unnamed: J7.4, U$2.22 (BOUT2)
unnamed: C11.1, U$2.25 (VCP)
unnamed: C10.1, U$2.2 (VG)
unnamed: C12.1, U$2.1 (CPA)
unnamed: C12.2, U$2.28 (CPB)
unnamed: R11.2, U$2.15 (ROSC)
unnamed: R12.1, U$2.12 (NFAULT)
unnamed: R10.2, U$2.13 (ISET)
OFF-GPIO3: J10.5 (SCL), U$5.P$1
SCK: J10.23 (SCLK)
STEP1: J10.38 (GP20), U$3.24 (STEP)
STEP2: J10.26 (CE1), U$2.24 (STEP)
STEP3: J10.10 (RXI), U$1.24 (STEP)

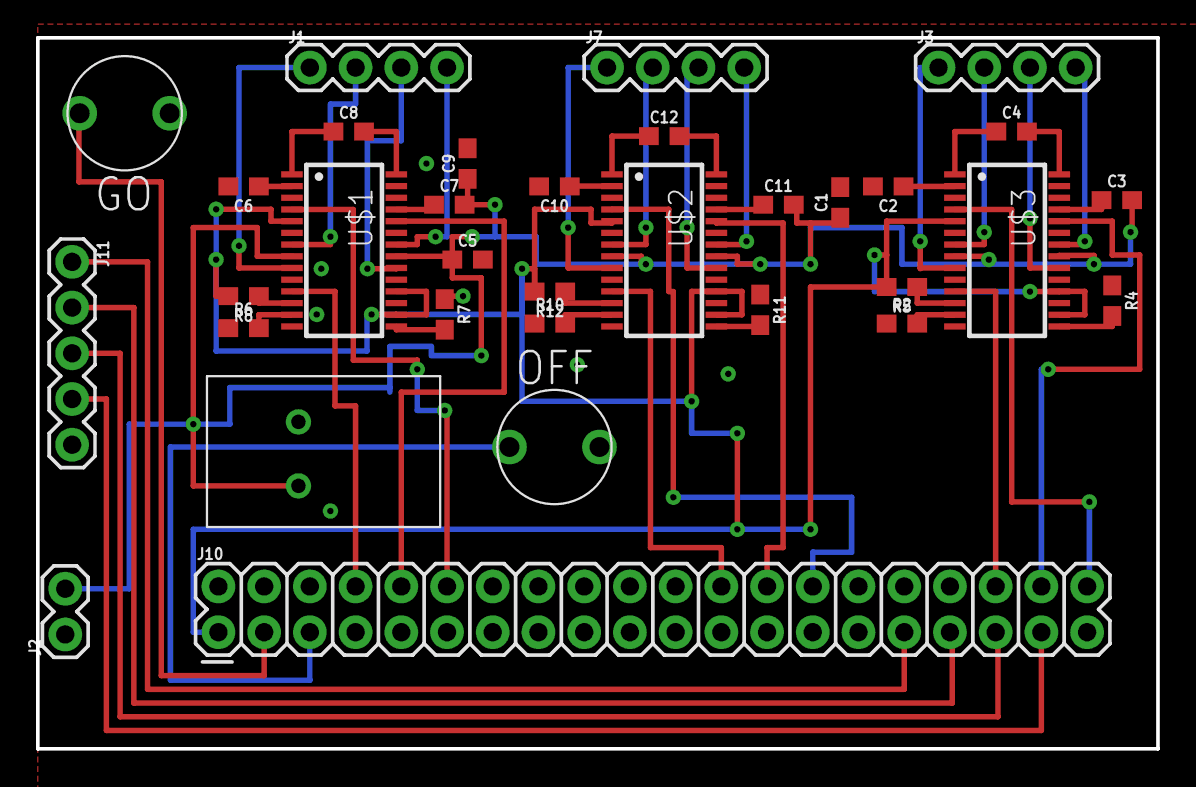
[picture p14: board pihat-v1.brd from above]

Board: 2 copper layers, 62.2 x 39.5 mm, 33 parts (0 on the bottom side), 52 nets.

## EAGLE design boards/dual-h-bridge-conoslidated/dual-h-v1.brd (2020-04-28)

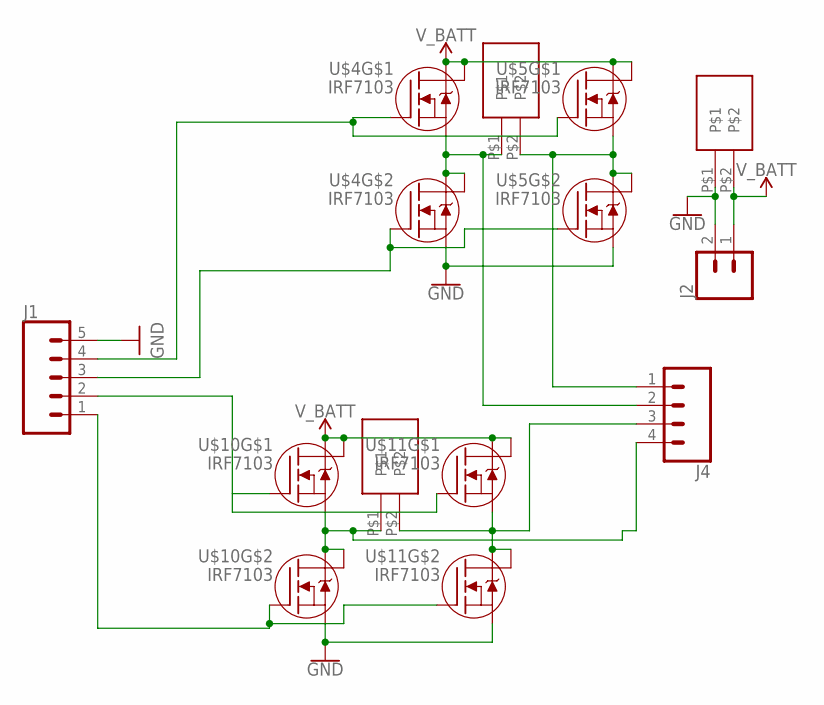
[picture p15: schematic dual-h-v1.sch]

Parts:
J1: CONN_05; 1X05
J2: CONN_02; 1X02
J4: CONN_04; 1X04
U$1, U$6, U$12: SPRING-TERMINAL
U$4, U$5, U$10, U$11: IRF7103; SO8-2

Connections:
GND: J1.5, J2.2, U$1.P$1, U$4.3 (S), U$5.3 (S), U$10.3 (S), U$11.3 (S)
unnamed: J4.4, U$10.1 (S), U$10.5 (D), U$10.6 (D), U$12.P$1
unnamed: J4.2, U$4.1 (S), U$4.5 (D), U$4.6 (D), U$6.P$1
unnamed: J4.1, U$5.1 (S), U$5.5 (D), U$5.6 (D), U$6.P$2
unnamed: J1.4, U$4.2 (G), U$5.2 (G)
unnamed: J1.1, U$10.4 (G), U$11.4 (G)
unnamed: J1.3, U$4.4 (G), U$5.4 (G)
unnamed: J4.3, U$11.1 (S), U$11.5 (D), U$11.6 (D), U$12.P$2
unnamed: J1.2, U$10.2 (G), U$11.2 (G)
V_BATT: J2.1, U$1.P$2, U$4.7 (D), U$4.8 (D), U$5.7 (D), U$5.8 (D), U$10.7 (D), U$10.8 (D), U$11.7 (D), U$11.8 (D)

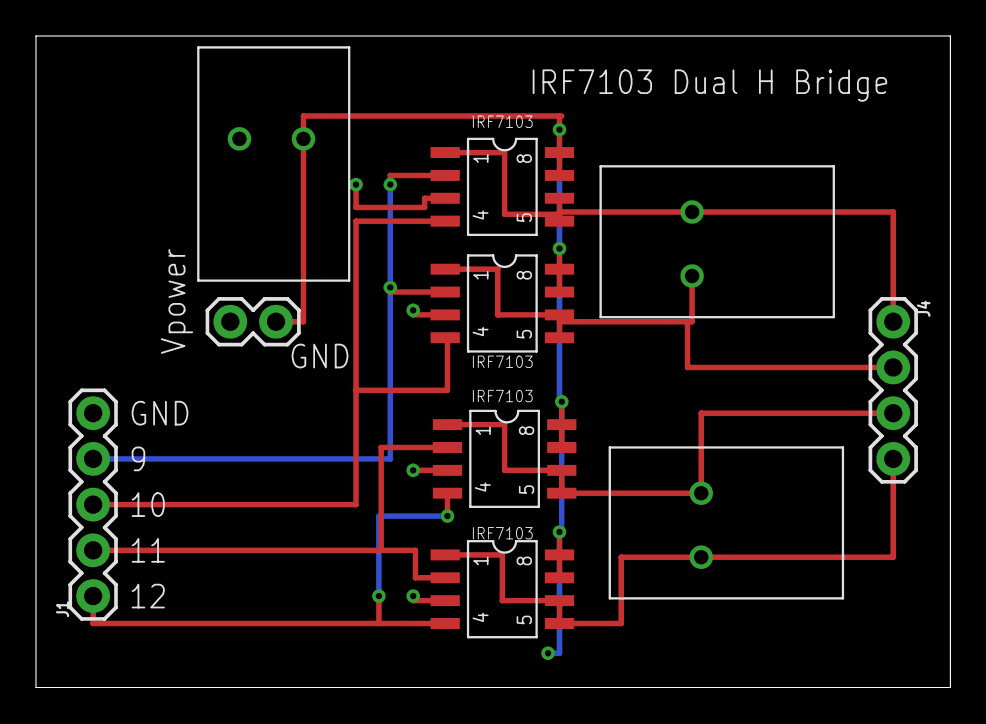
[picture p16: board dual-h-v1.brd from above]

Board: 2 copper layers, 50.8 x 36.2 mm, 10 parts (0 on the bottom side), 10 nets.

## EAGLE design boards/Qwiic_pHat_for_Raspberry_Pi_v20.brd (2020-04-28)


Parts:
C1, C3: 1.0uF; 0603
FD1, FD2, FD3, FD4: FIDUCIAL1X2; FIDUCIAL-1X2
FRAME1: FRAME-LETTER; CREATIVE_COMMONS
H1, H2, H3, H4, H5, H6: STAND-OFFTIGHT; STAND-OFF-TIGHT
J1, J6, J7, J8: Qwiic Right Angle; JST04_1MM_RA
J10: RASPBERRYPI-40-PIN-GPIO_PTH_NO_SHROUD; 2X20
JP1: PULLUP; SMT-JUMPER_3_2-NC_TRACE_NO-SILK
LOGO1: SFE_LOGO_NAME_FLAME.2_INCH; SFE_LOGO_NAME_FLAME_.2
LOGO2: REVISION
LOGO3: OSHW-LOGOS; OSHW-LOGO-S
R1, R2: 2.2k; 0603
U2: 3.3V/600mA; SOT23-5

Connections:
3.3V: C3.1, J1.2, J6.2, J7.2, J8.2, JP1.2, U2.5 (OUT)
5V: C1.1, J10.2 (5V), J10.4 (5V), U2.1 (IN), U2.3 (EN)
D4: J10.7 (GP4)
D5: J10.29 (GP5)
D6: J10.31 (GP6)
D12: J10.32 (GP12)
D13: J10.33 (GP13)
D16: J10.36 (GP16)
D17: J10.11 (GP17)
D18: J10.12 (GP18#)
D19: J10.35 (GP19)
D20: J10.38 (GP20)
D21: J10.40 (GP21)
D22: J10.15 (GP22)
D23: J10.16 (GP23)
D24: J10.18 (GP24)
D25: J10.22 (GP25)
D26: J10.37 (GP26)
D27: J10.13 (GP27)
GND: C1.2, C3.2, J1.1, J6.1, J7.1, J8.1, J10.6 (GND), J10.9 (GND), J10.14 (GND), J10.20 (GND), J10.25 (GND), J10.30 (GND), J10.34 (GND), J10.39 (GND), U2.2 (GND)
ID_SCL: J10.28 (ID_SC)
ID_SDA: J10.27 (ID_SD)
MISO: J10.21 (MISO)
MOSI: J10.19 (MOSI)
unnamed: JP1.3, R1.2
unnamed: JP1.1, R2.2
RX: J10.10 (RXI)
SCK: J10.23 (SCLK)
SCL: J1.4, J6.4, J7.4, J8.4, J10.5 (SCL), R2.1
SDA: J1.3, J6.3, J7.3, J8.3, J10.3 (SDA), R1.1
TX: J10.8 (TXO)

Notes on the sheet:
N. Seidle
Raspberry Pi Connector
V20
Qwiic Connectors
Power
A. England/Elias Santistevan
Pullup Jumper

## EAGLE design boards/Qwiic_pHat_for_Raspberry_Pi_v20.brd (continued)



Board: 2 copper layers, 65.0 x 30.5 mm, 28 parts (2 on the bottom side), 7 nets.

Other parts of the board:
U$1: QWIIC_11MM
U$2: I2C-()
U$3: PHAT0

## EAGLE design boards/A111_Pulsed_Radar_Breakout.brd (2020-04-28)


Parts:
C1, C5, C7: 0.1uF; 0603
C2, C6, C8, C9, C10: 1.0uF; 0603
C3, C4: 10pF; 0603
FD1, FD2, FD3, FD4: FIDUCIALUFIDUCIAL; FIDUCIAL-MICRO
FRAME1: FRAME-LETTER; CREATIVE_COMMONS
H1, H2: STAND-OFF
J2: CONN_08NO_SILK_FEMALE_PTH; 1X08_NO_SILK
J4: RASPBERRYPI-26-PIN-GPIO; 2X13
LOGO1: SFE_LOGO_NAME_FLAME.1_INCH; SFE_LOGO_NAME_FLAME_.1
LOGO2: OSHW-LOGOM; OSHW-LOGO-M
R1: 100k; 0603
U1: A111
U2: 1.8V; SOT23-5
U4: TXB0108DQSR; UFDFN-20
Y1: 26MHz; CRYSTAL-SMD-3.2X2.5MM

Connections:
1.8V: C1.1, C2.1, C5.1, C6.1, C7.1, C8.1, C10.1, U1.C2 (VIO_1), U1.C9 (VIO_2), U1.D1 (VIO_1), U1.D10 (VIO_2), U1.J1 (VBIAS), U1.J9 (VIO_3), U1.K9 (VIO_3), U2.5 (OUT), U4.5 (VCCA), U4.6 (OE)
5V: C9.1, J2.1, J4.2 (5V), J4.4 (5V), U2.1 (IN), U2.3 (EN), U4.16 (VCCB)
!CS!: U1.J2 (SS), U4.1 (A1)
!CS!_RPI: J2.8, J4.24 (CE0), U4.20 (B1)
ENABLE: U1.F10 (EN), U4.10 (A8)
ENABLE_RPI: J2.3, J4.13 (GP27), U4.11 (B8)
GND: C1.2, C2.2, C3.2, C4.1, C5.2, C6.2, C7.2, C8.2, C9.2, C10.2, J2.2, J4.6 (GND), J4.9 (GND), J4.14 (GND), J4.20 (GND), J4.25 (GND), R1.1, U1.A3 (GND), U1.A4 (GND), U1.A5 (GND), U1.A6 (GND), U1.A7 (GND), U1.A8 (GND), U1.A9 (GND), U1.B2 (GND), U1.B9 (GND), U1.B10 (GND), U1.C1 (GND), U1.C10 (GND), U1.D2 (GND), U1.D9 (GND), U1.E1 (GND), U1.E2 (GND), U1.E9 (GND), U1.E10 (GND), U1.F1 (GND), U1.F2 (GND), U1.F9 (GND), U1.G1 (GND), U1.G10 (GND), U1.H1 (GND), U1.H2 (GND), U1.H9 (GND), U1.J3 (GND), U1.J5 (GND), U1.J6 (GND), U1.J8 (GND), U1.K4 (GND), U1.K5 (GND), U1.K7 (GND), U2.2 (GND), U4.15 (GND), Y1.2 (3), Y1.4 (3)
INTERRUPT: R1.2, U1.K8 (INT), U4.9 (A7)
INTERRUPT_RPI: J2.4, J4.22 (GP25), U4.12 (B7)
MISO: U1.K3 (MISO), U4.3 (A3)
MISO_RPI: J2.6, J4.21 (MISO), U4.18 (B3)
MOSI: U1.K6 (MOSI), U4.8 (A6)
MOSI_RPI: J2.5, J4.19 (MOSI), U4.13 (B6)
unnamed: C3.1, U1.J10 (XIN), Y1.1
unnamed: C4.2, U1.H10 (XOUT), Y1.3 (2)
SCLK: U1.K2 (SCLK), U4.2 (A2)
SCLK_RPI: J2.7, J4.23 (SCLK), U4.19 (B2)

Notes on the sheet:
VIO1a,b -- C2, D1
VIO2a,b -- C9, D10
VIO3a,b -- J9, K9
Jim Lindblom
Revised By: Elias Santistevan
v10
Pulsed Radar - A111
Logic Level Translator
Decoupling Capacitors
Raspberry Pi and 8-Pin Header
Voltage Regulator
40 pin is backwards compatible with 26 pin header.
VCC Range 1.7V - 1.89V



Board: 2 copper layers, 33.0 x 39.4 mm, 44 parts (25 on the bottom side), 17 nets.

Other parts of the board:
LOGO3: SFE_LOGO_NAME_FLAME.1_INCH; SFE_LOGO_NAME_FLAME_.1
U$1, U$9: A111_PULSED_RADAR9
U$2, U$10: SCLK3
U$3, U$11: MISO4
U$4: MOSI5
U$5: INT8
U$6, U$18: EN9
U$7, U$15: GND0
U$8, U$16: 5V1
U$12: PI_DISPLAY9
U$13, U$17: #CS9

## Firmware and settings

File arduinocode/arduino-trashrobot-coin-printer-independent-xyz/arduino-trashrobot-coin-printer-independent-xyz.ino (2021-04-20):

char coin[] = "GGGGGGGGGGGGGGGEEEEHEEEEEADDDDGGBBBBBBHHHHFAAAAAAADDDHBBFCCCHBFDFDHHFAAAAAAHADDFDBBBBBEEECCCHHHHFFFHAFDDDHAAECCCGAAHADDHBFFFFFHHFAAAAAAAFFFDDDDAAAFFFBBBHFFFFFFFFFFFFFGGGGGGGGGGGGGGGGGGGGGGGGGGGGGGHFAAAAAAADDDHBBFCCCHBFDFDHHAAAAAHADDFDBBBBFCCCHHHHHFAAAAAAADDDHBBFCCCHHHBBFCCCHHHHHAAAAAHADDFDBBBBFCCCHHHHHEEEEEADDDDGGBBBBBBHHHEEEEEEEEEGGGGGGGGGGGGGGG";


int delayus = 500;//delayMicroseconds(delayus);

int unit = 100;
int side = unit;

//these are the pin numbers of the buttons on the controller.  Connect to ground to activate.
int xleftPin = 7;
int xrightPin = 10;
int yawayPin = 9;
int ytowardsPin = 8;
int zdownPin = 11;
int zupPin = 12;

int goPin = 6;
int stopPin = 5;

//connect these pins to the MP6500 stepper motor control board:
int dirPin3 = 19;
int stepPin3 = 18;
int enPin3 = 17;
int dirPin1 = 16;
int stepPin1 = 15;

int enPin1 = 13;

int dirPin2 = 2;
int stepPin2 = 3;
int enPin2 = 4;

boolean xleftBool = false;
boolean xrightBool = false;
boolean yawayBool = false;
boolean ytowardsBool = false;
boolean zdownBool = false;
boolean zupBool = false;
boolean goBool = false;
boolean stopBool = false;

int select = 0;

void setup() {

    pinMode(xleftPin,INPUT_PULLUP); 
    pinMode(xrightPin,INPUT_PULLUP); 
    pinMode(yawayPin,INPUT_PULLUP); 
    pinMode(ytowardsPin,INPUT_PULLUP); 
    pinMode(zdownPin,INPUT_PULLUP); 
    pinMode(zupPin,INPUT_PULLUP); 
    pinMode(goPin,INPUT_PULLUP); 
    pinMode(stopPin,INPUT_PULLUP); 

    pinMode(dirPin1,OUTPUT);
    pinMode(stepPin1,OUTPUT);
    pinMode(enPin1,OUTPUT);
    pinMode(dirPin2,OUTPUT);
    pinMode(stepPin2,OUTPUT);
    pinMode(enPin2,OUTPUT);
    pinMode(dirPin3,OUTPUT);
    pinMode(stepPin3,OUTPUT);
    pinMode(enPin3,OUTPUT);

    digitalWrite(dirPin1,LOW);
    digitalWrite(stepPin1,LOW);
    digitalWrite(enPin1,HIGH);
    digitalWrite(dirPin2,LOW);
    digitalWrite(stepPin2,LOW);
    digitalWrite(enPin2,HIGH);
    digitalWrite(dirPin3,LOW);
    digitalWrite(stepPin3,LOW);
    digitalWrite(enPin3,HIGH);
    
    Serial.begin(9600);

}

void loop() { 
  
  
  xleftBool = !digitalRead(xleftPin);
  xrightBool = !digitalRead(xrightPin);
  yawayBool = !digitalRead(yawayPin);
  ytowardsBool = !digitalRead(ytowardsPin);
  zdownBool = !digitalRead(zdownPin);
  zupBool = !digitalRead(zupPin);
  goBool = !digitalRead(goPin);
  stopBool = !digitalRead(stopPin);
  
   //Serial.println(goBool); 
  if(goBool){
      printCoin(); 
  }

  if(xleftBool){
     moveLeft(1);
  }
  if(xrightBool){
     moveRight(1);
  }
  if(zdownBool){
    moveUp(1); 
  }
  if(zupBool){
    moveDown(1); 
  }
  if(yawayBool){
    moveAway(1);
  }
  if(ytowardsBool){
    moveTowards(1);
 }
}

void moveLeft(int nSteps){
     digitalWrite(dirPin1,LOW);
     digitalWrite(enPin1,LOW);
     
     for(int index = 0;index < nSteps;index++){
       digitalWrite(stepPin1,HIGH);
       delayMicroseconds(delayus); 
       digitalWrite(stepPin1,LOW);
       delayMicroseconds(delayus); 

     }          
     digitalWrite(enPin1,HIGH);   
     digitalWrite(enPin2,HIGH);   
}

void moveRight(int nSteps){
     digitalWrite(dirPin1,HIGH);
     digitalWrite(enPin1,LOW);
    
     for(int index = 0;index < nSteps;index++){
       digitalWrite(stepPin1,HIGH);
       delayMicroseconds(delayus); 
       digitalWrite(stepPin1,LOW);
       delayMicroseconds(delayus); 

     }          
     digitalWrite(enPin1,HIGH);   
     digitalWrite(enPin3,HIGH);   

}

void moveDown(int nSteps){
     digitalWrite(dirPin3,HIGH);
     digitalWrite(enPin3,LOW);
     
     for(int index = 0;index < nSteps;index++){
       digitalWrite(stepPin3,HIGH);
       delayMicroseconds(delayus); 
       digitalWrite(stepPin3,LOW);
       delayMicroseconds(delayus); 
     }          
     digitalWrite(enPin1,HIGH);   
     digitalWrite(enPin3,HIGH);   

}

void moveUp(int nSteps){
     digitalWrite(dirPin3,LOW);
     digitalWrite(enPin3,LOW);     
     for(int index = 0;index < nSteps;index++){
       digitalWrite(stepPin3,HIGH);
       delayMicroseconds(delayus); 
       digitalWrite(stepPin3,LOW);
       delayMicroseconds(delayus); 
     }          
     digitalWrite(enPin3,HIGH);    
     digitalWrite(enPin1,HIGH);

}

void moveAway(int nSteps){
     digitalWrite(dirPin2,LOW);
     digitalWrite(enPin2,LOW);
     
     for(int index = 0;index < nSteps;index++){
       digitalWrite(stepPin2,HIGH);
       delayMicroseconds(delayus); 
       digitalWrite(stepPin2,LOW);
       delayMicroseconds(delayus); 
     }          
     digitalWrite(enPin2,HIGH);   
}

void moveTowards(int nSteps){
     digitalWrite(dirPin2,HIGH);
     digitalWrite(enPin2,LOW);
     
     for(int index = 0;index < nSteps;index++){
       digitalWrite(stepPin2,HIGH);
       delayMicroseconds(delayus); 
       digitalWrite(stepPin2,LOW);
       delayMicroseconds(delayus); 
     }          
     digitalWrite(enPin2,HIGH);   
}


void geometronAction(char action){
  stopBool = !digitalRead(stopPin);
  if(action == 'a'){
     moveRight(side);
  }
  if(action == 'b'){
     moveLeft(side);
  }
  if(action == 'c'){
    moveAway(side);
  }
  if(action == 'd'){
    moveTowards(side);
  }
  if(action == 'e'){
    moveUp(side);
  }
  if(action == 'f'){
    moveDown(side);
  }
  if(action == 'g'){
    side /= 2;
  }
  if(action == 'h'){
    side *= 2;
  }
  if(action == 'A'){
    geometronSequence("ggdhhef");
  }
  if(action == 'B'){
    geometronSequence("ggchhef");
  }
  if(action == 'C'){
    geometronSequence("ggbhhef");
  }
  if(action == 'D'){
    geometronSequence("ggahhef");
  }
  if(action == 'E'){
    geometronSequence("ggdhh");
  }
  if(action == 'F'){
    geometronSequence("ggchh");
  }
  if(action == 'G'){
    geometronSequence("ggbhh");
  }
  if(action == 'H'){
    geometronSequence("ggahh");
  }
}


void printCoin(){
   for(int index = 0;index <= sizeof(coin);index++){
    if(!stopBool){
      geometronAction(coin[index]);    
    }
   }  
}


void geometronSequence(String glyph){
  //for loop thru the String
  int index = 0;
  for(index = 0;index < glyph.length();index++){
    if(!stopBool){
      geometronAction(glyph.charAt(index));      
    }
   }
}

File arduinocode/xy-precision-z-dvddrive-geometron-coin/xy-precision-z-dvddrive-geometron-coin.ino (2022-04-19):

char coin[] = "GGGGGGGGGGGGGGGEEEEHEEEEEADDDDGGBBBBBBHHHHFAAAAAAADDDHBBFCCCHBFDFDHHFAAAAAAHADDFDBBBBBEEECCCHHHHFFFHAFDDDHAAECCCGAAHADDHBFFFFFHHFAAAAAAAFFFDDDDAAAFFFBBBHFFFFFFFFFFFFFGGGGGGGGGGGGGGGGGGGGGGGGGGGGGGHFAAAAAAADDDHBBFCCCHBFDFDHHAAAAAHADDFDBBBBFCCCHHHHHFAAAAAAADDDHBBFCCCHHHBBFCCCHHHHHAAAAAHADDFDBBBBFCCCHHHHHEEEEEADDDDGGBBBBBBHHHEEEEEEEEEGGGGGGGGGGGGGGG";

//char coin[]= "hefgahefg";

int unit = 100;
int side = unit;


int controller = 0;
int delta = 16;

int AIN1 = 7;
int AIN2 = 8;
int PWMA = 9;

int dirPin1 = 2;
int stepPin1 = 3;
int enPin1 = 4;

int dirPin2 = 5;
int stepPin2 = 6;
int enPin2 = 10;


//there is a ladder of 9 10k resistors from 5v to ground, and the intermediate nodes all connect to buttons which connect to an analog pin which has a 1 megaohm pull down resistor
int value1 = 114;
int value2 = 2*114;
int value3 = 3*114;
int value4 = 4*114;
int value5 = 5*114;
int value6 = 6*114;
int value7 = 7*114;
int value8 = 8*114;

int button = 0;  //0 means no press, 1 is start, 2 is stop, 3 is left, 4 is back 5 is forward, 6 is right, 7 is down 8 is up


int delayus = 500;//delayMicroseconds(delayus);

int z = 0;
int zdelay = 1500;// microseconds 1000 ms / 512 steps = 2 ms/step


boolean goBool = false;
boolean stopBool = false;

void setup() {
  // put your setup code here, to run once:
  controller = analogRead(A0);

    pinMode(AIN1,OUTPUT);
    pinMode(AIN2,OUTPUT);
    pinMode(PWMA,OUTPUT);
    
    analogWrite(PWMA,0);
    digitalWrite(AIN1,LOW);
    digitalWrite(AIN2,LOW);


    pinMode(dirPin1,OUTPUT);
    pinMode(stepPin1,OUTPUT);
    pinMode(enPin1,OUTPUT);
    pinMode(dirPin2,OUTPUT);
    pinMode(stepPin2,OUTPUT);
    pinMode(enPin2,OUTPUT);

    digitalWrite(dirPin1,LOW);
    digitalWrite(stepPin1,LOW);
    digitalWrite(enPin1,HIGH);
    digitalWrite(dirPin2,LOW);
    digitalWrite(stepPin2,LOW);
    digitalWrite(enPin2,HIGH);

  
  Serial.begin(9600);

}

void loop() {
  // put your main code here, to run repeatedly:
  controller = analogRead(A0);

  if(controller > value1 - delta && controller < value1 + delta){
     button = 1;   
  }
  if(controller > value2 - delta && controller < value2 + delta){
     button = 2;   
  }

  if(controller > value3 - delta && controller < value3 + delta){
     button = 3;   
  }

  if(controller > value4 - delta && controller < value4 + delta){
     button = 4;    
  }

  if(controller > value5 - delta && controller < value5 + delta){
     button = 5;   
  }

  if(controller > value6 - delta && controller < value6 + delta){
     button = 6;   
  }

  if(controller > value7 - delta && controller < value7 + delta){
     button = 7;   
  }

  if(controller > value8 - delta && controller < value8 + delta){
     button = 8;         
  }


  if(controller < 50){
     button = 0;   
  }

   if(button == 1){
    //Serial.println("start");  
    stopBool = false;
    printCoin();
   }
   if(button == 2){
    //Serial.println("stop");
    
   }
   if(button == 3){
    //Serial.println("left");
    moveLeft(1);
   }
   if(button == 4){
    //Serial.println("back");
    moveAway(1);
   }
   if(button == 5){
    //  Serial.println("forward");
      moveTowards(1);
   }
   if(button == 6){
      //Serial.println("right");
      moveRight(1);
   }
   if(button == 7){
      z = z - 1;
      if(z < -255){
        z = -255;
      }
      delayMicroseconds(delayus);
//      Serial.println("down");
   }
    if(button == 8){
      //up
      z = z + 1;
      if(z > 255){
        z = 255;
      }
      delayMicroseconds(delayus);
//      Serial.println("up");
   }

//   Serial.println(button); 


   if(z >= 0){
      digitalWrite(AIN2,LOW);
      digitalWrite(AIN1,HIGH);      
   }
   else{
      digitalWrite(AIN1,LOW);      
      digitalWrite(AIN2,HIGH);
   }      
   analogWrite(PWMA,abs(z));
   //Serial.println(z);

}


void moveUp(int nSteps){

  for(int index = 0;index < nSteps;index++){
    z += 1;
    if(z>255){
      z=255;
    }
    if(z >= 0){
      digitalWrite(AIN2,LOW);
      digitalWrite(AIN1,HIGH);      
    }
    else{
      digitalWrite(AIN1,LOW);      
      digitalWrite(AIN2,HIGH);
    }      
    analogWrite(PWMA,abs(z)); 
    delayMicroseconds(zdelay); 
  }

}

void moveDown(int nSteps){

  for(int index = 0;index < nSteps;index++){
    z -= 1;
    if(z < 0){
      z=0;
    }
    if(z >= 0){
      digitalWrite(AIN2,LOW);
      digitalWrite(AIN1,HIGH);      
    }
    else{
      digitalWrite(AIN1,LOW);      
      digitalWrite(AIN2,HIGH);
    }      
    analogWrite(PWMA,abs(z)); 
    delayMicroseconds(zdelay); 
  }
}

void moveLeft(int nSteps){
     digitalWrite(dirPin1,LOW);
     digitalWrite(enPin1,LOW);
     
     for(int index = 0;index < nSteps;index++){
       digitalWrite(stepPin1,HIGH);
       delayMicroseconds(delayus); 
       digitalWrite(stepPin1,LOW);
       delayMicroseconds(delayus); 

     }          
     digitalWrite(enPin1,HIGH);   
     digitalWrite(enPin2,HIGH);   
}

void moveRight(int nSteps){
     digitalWrite(dirPin1,HIGH);
     digitalWrite(enPin1,LOW);
    
     for(int index = 0;index < nSteps;index++){
       digitalWrite(stepPin1,HIGH);
       delayMicroseconds(delayus); 
       digitalWrite(stepPin1,LOW);
       delayMicroseconds(delayus); 

     }          
     digitalWrite(enPin1,HIGH);   

}


void moveAway(int nSteps){
     digitalWrite(dirPin2,LOW);
     digitalWrite(enPin2,LOW);
     
     for(int index = 0;index < nSteps;index++){
       digitalWrite(stepPin2,HIGH);
       delayMicroseconds(delayus); 
       digitalWrite(stepPin2,LOW);
       delayMicroseconds(delayus); 
     }          
     digitalWrite(enPin2,HIGH);   
}

void moveTowards(int nSteps){
     digitalWrite(dirPin2,HIGH);
     digitalWrite(enPin2,LOW);
     
     for(int index = 0;index < nSteps;index++){
       digitalWrite(stepPin2,HIGH);
       delayMicroseconds(delayus); 
       digitalWrite(stepPin2,LOW);
       delayMicroseconds(delayus); 
     }          
     digitalWrite(enPin2,HIGH);   
}


void geometronAction(char action){

  controller = analogRead(A0);
  if(controller > value2 - delta && controller < value2 + delta){
     button = 2;
     stopBool = true;   
  }

  if(action == 'a'){
     moveRight(side);
  }
  if(action == 'b'){
     moveLeft(side);
  }
  if(action == 'c'){
    moveAway(side);
  }
  if(action == 'd'){
    moveTowards(side);
  }
  if(action == 'e'){
    moveUp(side);
  }
  if(action == 'f'){
    moveDown(side);
  }
  if(action == 'g'){
    side /= 2;
  }
  if(action == 'h'){
    side *= 2;
  }
  if(action == 'A'){
    geometronSequence("ggdhhhefg");
  }
  if(action == 'B'){
    geometronSequence("ggchhhefg");
  }
  if(action == 'C'){
    geometronSequence("ggbhhhefg");
  }
  if(action == 'D'){
    geometronSequence("ggahhhefg");
  }
  if(action == 'E'){
    geometronSequence("ggdhh");
  }
  if(action == 'F'){
    geometronSequence("ggchh");
  }
  if(action == 'G'){
    geometronSequence("ggbhh");
  }
  if(action == 'H'){
    geometronSequence("ggahh");
  }
}
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

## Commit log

2019-11-13 trash robot 5 now has most recent versions of all files, is the official trash robot repository now
    [dualHbridge-v4bom.xlsx, dualHbridge-v5.brd, dualHbridge-v5.sch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]
2019-11-13 files mostly ready to order now
    [dualHbridge-v4bom.xlsx, dualHbridge-v5bom.xlsx, unoshield-v5-bom.xlsx]
2019-11-17 added readme with linked bom
    [dualHbridge-v5.brd, dualHbridge-v5.sch, dualHbridge-v5bom.xlsx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]
2019-11-23 better links, localized dna and repilcatro
    [unoshield-v5.brd]
2019-11-30 added button stepper control
2020-04-28 more board desings, and arduino code
    [A111_Pulsed_Radar_Breakout.brd, A111_Pulsed_Radar_Breakout.sch, Qwiic HAT for Raspberry Pi.brd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]
2020-04-29 pihat streamlined, largely laid out
    [pihat-v1.brd, pihat-v1.sch]
2020-04-30 pihat v2 for pololu boards with potentiometers
    [pihat-v2.brd, pihat-v2.sch]
2020-05-01 hat improvements, lots more arduino code
    [pihat-v2.brd]
2020-05-01 small tweaks to pi hat
    [pihat-v2.brd]
2020-11-19 added very useful arduino code
    [pihat-v2.brd]
2020-11-19 git, like all things made by software scum, is horrible technology for horrible people. updated shield boards
    [arduino-shield-xyz-stepper.brd, arduino-shield-xyz-stepper.sch, eight-button-sheild.brd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]
2020-11-19 added some breakout plated holes for A0-A6 and power pins to button board
    [eight-button-sheild.brd, eight-button-sheild.sch]
2020-12-08 xyz stepper control
    [arduino-shield-xyz-stepper.brd, arduino-shield-xyz-stepper.sch, eight-button-sheild.brd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]
2021-01-27 main program updates and new version of pcb updates
    [arduino-shield-xyz-stepper-v2.brd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]
2021-01-31 better robot code, new board version
    [arduino-shield-xyz-stepper-v3.brd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]
2021-01-31 C is an evil language for evil people :( but maybe memory problems are solved
    [xyz-stepper-control-direct-v3-charnotstring.ino]
2021-02-18 smaller coin for default
    [arduino-shield-xyz-stepper-v4.brd, arduino-shield-xyz-stepper-v4.sch]
2021-03-02 knob buttons code tweaks
2021-04-03 arduino bottle caps printer!!!
2022-02-02 uno shield board version 6
    [unoshield-v6.brd, unoshield-v6.sch]
2022-02-07 shield tweaks
    [unoshield-v6-bom.xlsx, unoshield-v6.brd, unoshield-v6.sch]
2022-02-08 gerbers zip made and submitted to pcbway
    [unoshield-v6.brd]
2022-02-08 saved screen shot of new board
2022-04-19 geometron coin printer with DVD drive micro z
2022-04-20 new arduino shield board with dual h bridge and 2 stepper drivers
    [arduino-shield-xyzhbridge-stepper-v1.brd, arduino-shield-xyzhbridge-stepper-v1.sch]
2022-04-20 finishing touches on a draft of the full control board with slimezistor etc
    [arduino-shield-xyzhbridge-stepper-v1.brd, arduino-shield-xyzhbridge-stepper-v1.sch]
2022-04-21 two new boards, xyz and slime and xyzhbridge and slime
    [arduino-shield-xyz-slime-stepper-v1.brd, arduino-shield-xyz-slime-stepper-v1.sch, arduino-shield-xyzhbridge-stepper-v1.brd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]

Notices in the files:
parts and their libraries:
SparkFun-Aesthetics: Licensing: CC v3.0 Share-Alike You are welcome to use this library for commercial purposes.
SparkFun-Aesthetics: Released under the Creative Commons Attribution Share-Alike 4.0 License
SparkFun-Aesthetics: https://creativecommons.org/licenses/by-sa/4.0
